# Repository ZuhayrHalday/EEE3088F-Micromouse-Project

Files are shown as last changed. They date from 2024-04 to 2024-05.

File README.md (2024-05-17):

# MicroMouse Project: Sensing and Power Subsystems

Welcome to the MicroMouse Project repository! The problem this entire project deals with is to design, build, and test a fully-functioning MicroMouse robot. Akin to the mice in the famous Kerplunk Experiments, a MicroMouse robot should be able to solve a maze using the shortest and fastest route possible. This README provides an overview of the project and subsystem descriptions.

## Project Overview

The goal of this project is to build key subsystems for a simplified MicroMouse, a maze-solving robot. These will be designed, manufactureed, and tested during the course of a semester.

## Subsystems

### 1. Power Subsystem (more info [here](https://github.com/ZuhayrHalday/EEE3088F-Micromouse-Project/tree/main/Power%20Subsystem))
- **Purpose:** Provide power to the entire system.
- **Key Functions:**
  - Operate two motors (each drawing up to 200mA).
  - Charge the battery from a 5V input.
  - Provide battery voltage information to the processor.
  - Include an ON/OFF switch with specific power draw requirements.
- **Connections:**
  - JST PH 2mm pin pitch connector for the battery.
  - 2x8 (2.54mm pin pitch) pin header for interfacing with the motherboard.<br />
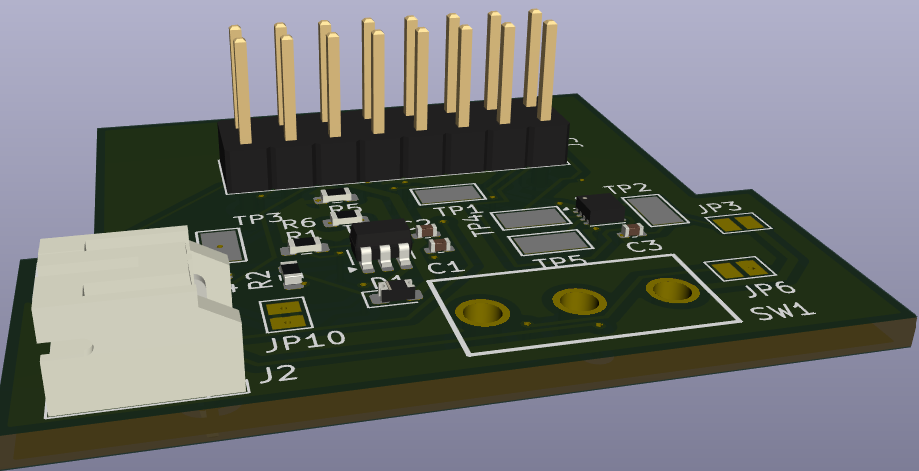
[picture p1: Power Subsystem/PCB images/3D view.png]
  <br />

### 2. Sensing Subsystem (more info [here](https://github.com/ZuhayrHalday/EEE3088F-Micromouse-Project/tree/main/Sensing%20Subsystem))
- **Purpose:** Detect obstacles in the robot's path.
- **Key Functions:**
  - Detect obstacles in front and on the sides of the robot using infrared LED's and photodiodes to sense reflective obstacles.
  - Use power-saving features when not in operation.
  - Provide reliable detection data to the processor.
  - Interface with processor LEDs to indicate detected obstacles.
- **Connections:**
  - 2x14 (2.54mm pin pitch) pin header for interfacing with the motherboard.<br />
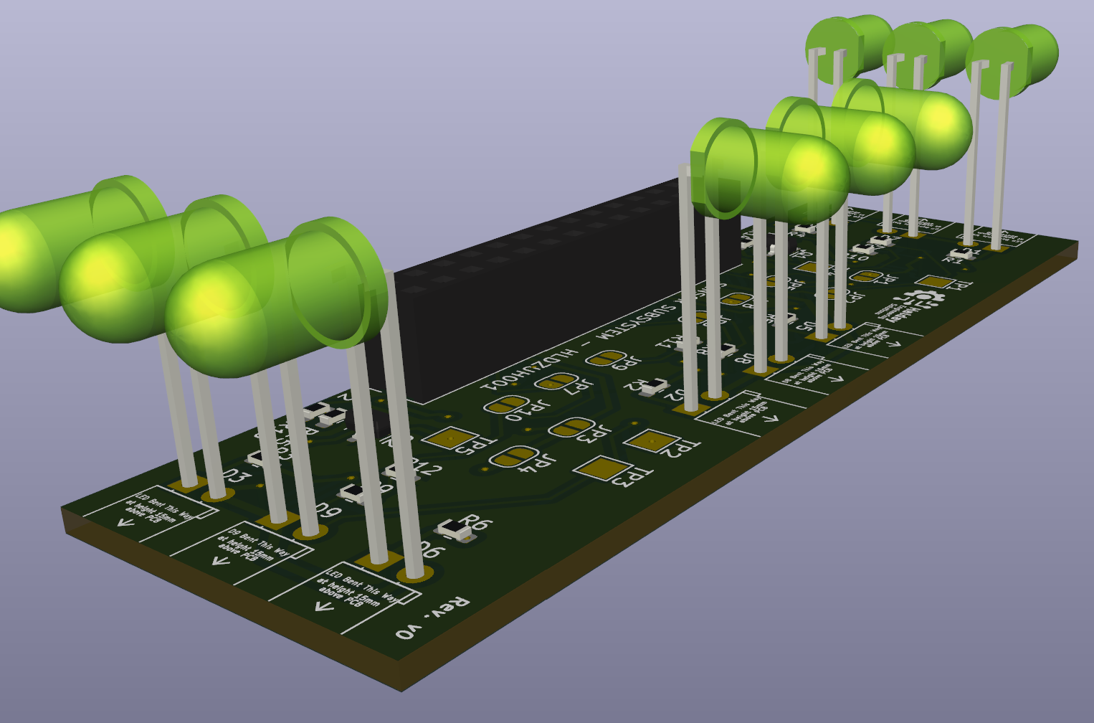
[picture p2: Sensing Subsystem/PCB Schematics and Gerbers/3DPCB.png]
  <br />

### 3. The Motherboard
The Motherboard houses all subsystems and addresses the movement and ‘brain’ aspects of the project. The
wheels and motors of the MicroMouse are attached to the Motherboard PCB, which also mounts an STM32L476
microcontroller to manage input and output logic. Pin headers are provided for interfacing with other subsystems. This subsystem has been provided beforehand, and was not designed as a part of this project.

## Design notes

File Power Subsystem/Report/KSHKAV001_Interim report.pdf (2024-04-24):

# Interim Design Report

Micromouse Power Subsystem


Prepared by:
Kavya Kaushik

Prepared for:
EEE3088F
Department of Electrical Engineering University of Cape Town

April 21, 2024

# Declaration

1. I know that plagiarism is wrong. Plagiarism is to use another’s work and pretend that it is one’s own.
2. I have used the IEEE convention for citation and referencing. Each contribution to, and quotation in, this report from the work(s) of other people has been attributed, and has been cited and referenced.
3. This report is my own work.
4. I have not allowed, and will not allow, anyone to copy my work with the intention of passing it off as their own work or part thereof.

Sign:

Date: 21 April 2024

ii

# Contents

1 Introduction | 1
2 Requirements Analysis | 2
3 Subsystem Design | 5
4 Acceptance Testing | 10

iii

# Chapter 1

# Introduction

### 1.1 Problem Description

The project focuses on the development of an autonomous maze-solving robot, commonly known as a micro-mouse. the project aims to integrate power, sensing and control to operate this robot. This report is focused on the design of the power subsystem, with the goal of supplying uninterrupted regular current to the micro-mouse to ensure its safe and effective operation. The design involves considering specific design requirements and specifications while comprising of integration with the sensing and control subsystems while adhering to the specified limitations.

### 1.2 Scope and Limitations

Scope | Limitations
Component selection and sizing: Select appro-priate components considering such as voltage, current ratings, energy capacity, sizing, effi-ciency and costs | Limited budget which impacts the cost and quality of components that can be used
Power distribution and regulation: Ensuring stable voltage supply to various subsystems and components of the robot, depending on specifications of the components and specifica-tions of the rest of the system for integration | Constraints on the size of the components to ensure it fits onto the motherboard and along with the other subsystems
Implement a battery management system to control the charging and discharging for opti-mal battery performance | Limitations to the energy capacity of the sys-tem and discharge rates of the battery as per requirements
Ensure that the power subsystem can be inte-grated with the remaining system | Constraints about placement and connections of the other subsystems to ensure integration
Implement testing and fault tolerance mecha-nisms to ensure reliability of the circuit and to verify its functionality and performance during different conditions. | Limitations resources for sufficient testing and validation

Table 1.1: Scope and Limitations of the Power Subsystem

### 1.3 GitHub Link

Project GitHub repository: Github Link (https://github.com/ZuhayrHalday/EEE3088F-Micromouse-Project)

# Chapter 2

# Requirements Analysis

### 2.1 Requirements

The requirements for a micro-mouse power module are described in Table 2.1.

Table 2.1: User and functional requirements of the power subsystem.

Requirement ID | Description
FR01 | Supply power to the battery using voltage from a logic-based micro controller power supply to charge the battery
FR02 | Regulate the charging and discharging of the battery to ensure overcharging, temperature monitoring and over-discharge protection by regulating the current drawn from the battery
FR03 | Maximise battery life by allowing minimal power consumption
UR01 | Supply regulated current to both motors to drive them
UR02 | Provide an analogue signal that indicates the battery’s state of charge from the battery voltage that can be sent to the ADC of the micro controller
UR03 | Contains a switch to turn the power supply ON/OFF
FR04 | The PCB board fits onto the pin headers of the motherboard
FR05 | The PCB designed with an size suitable for the micro mouse robot
UR04 | The PCB cost is within the budget specified
UR05 | All components in stock with JLCPBCB
FR06 | Battery has a maximum and minimum current draw in ON and OFF state

### 2.2 Specifications

The specifications, refined from the requirements in Table 2.1, for the micromouse power module are described in Table 2.2.

Table 2.2: Specifications of the sensing subsystem derived from the requirements in Table 2.1.

Specification ID | Description
SP01 | The battery used is a LiPo 800mAh 3.7V battery
SP02 | The battery is charged is a 5V input pin from a microcontroller
SP03 | The battery is kept at a max discharge rate of 0.5C(capacity) implying that a fully charged battery takes 2 hours to fully discharge
SP04 | The maximum current drawn by the battery is 400mA
SP05 | The circuit needs to supply current to two motors with a maximum current draw of 200 mA each

2.3. Testing Procedures
Specification ID | Description
SP06 | The analog output needs to be within the range of to meet the STM32L476 microcontroller’s ADC range
SP07 | The battery can only draw less than 500uA when the switch is in the OFF state
SP08 | The battery can draw the peak current of 400mA during the ON state of the switch
SP09 | A JST PH 2mm pin pitch is used as the connector for the battery
SP10 | A 2x8 (2.54mm pin pitch) pin header is for the power subsystem
SP11 | The connector needs to be centered in a tab and have a maximum width of 35mm and a minimum height of 18mm
SP12 | The circuit uses PWM integration with microcontroller
SP13 | Both PCB boards need to be manufactured within $30

### 2.3 Testing Procedures

A summary of the testing procedures detailed in chapter 4 is given in Table 2.3.

Table 2.3: Testing procedures for Power Subsystem

Acceptance Test ID | Description
AT01 | Battery Voltage supply check
AT02 | Switching circuit ON state
AT03 | Switching circuit OFF state
AT04 | Input pin connection of 5V
AT05 | Battery charging operation
AT06 | Analog output supply of battery state of charge
AT07 | Current output into motors test
AT08 | Power supply of motors test
AT09 | PCB dimensions test
AT10 | Project budget test

2.4. Traceability Analysis

### 2.4 Traceability Analysis

The show how the requirements, specifications and testing procedures all link, Table 2.4 is provided.

Table 2.4: Requirements Traceability Matrix

# | Requirements | Specifications | Acceptance Test

1 2 3 4 5 6 7 | FR01 FR02, FR03, FR06 UR01 UR02 FR04 UR04 FR05 | SP01, SP02 SP03, SP04, SP07, SP08 SP05 SP06 SP10 SP13 SP11 | AT01, AT04 AT02, AT03, AT05 AT07, AT08 AT06 AT09 AT10 AT09

Traceability Analysis 1 - FR01 is this from which SP01, SP02, can be derived. To test this AT01, AT04 is suggested to ensure successful operation of the battery

Traceability Analysis 2 - From FR02,FR03, FR04, SP03, SPO4, SP07 and SP08 can be derived to properly check the switching circuit and charging and discharging.

Traceability Analysis 3 - From UR01, SP05 can be derived to check the successful operation of motors which can be tested using AT07, AT08

Traceability analysis 4 - From UR02, SP06 can be derived and the output analoge signal which can be tested with AT06.

Traceability Analysis 5 - From FR04 SP10 can be derived and test AT09 can be conducted to test the implementation of pin header

Traceability analysis 6 - From UR04, SP13 can be derived to check the budgeting of PCB which can be tested using A10

# Chapter 3

# Subsystem Design

### 3.1 Design Decisions

### 3.1.1 Battery Management System

The battery used as per specification , and has a voltage range between 3.0V to 4.2V with a recommended Lithium Polymer charger[[reference]. The battery management system needs to consider the requirements such to ensure functionality and circuit protection, for which a battery management IC can be used.

Based on specification SP01, the battery management ICs that can support all functionality and are in stock are listed in Table 3.1.

Table 3.1: Component specifications for the battery management system
Item | Component | Voltage regulation | Charge current | Cost
1 | MCP73831T-2ATI/OT | 4.2V, 4.35, 4.40V, 4.50V | 15mA to 500mA(prog*) | 0.9945
2 | BQ24295 | 4.55 V – 5.5 V | 1792mA for V = 3.8V | 0.7635
3 | MCP73833/4 | 4.2V, 4.35V, 4.4V, 4.5V | 1A (prog*) | 1.5330
4 | MCP73837/8 | 4.20V, 4.35V, 4.4V or 4.5V | 15 mA – 1000 mA (prog*) | 2.7900

*prog means the value is programmable

From Table 3.1, it can be seen that Component 3 draws a much larger current compared to the other three components, amongst which Component 1 is the cheapest. Therefore the MCP73831T component is finalised as the battery charging IC since it supports the voltage range of the battery which is 4.2V, it can handle the current drawn by the battery which is 400mA and it is the most cost-effective.

The datasheet is used to implement the circuit accoridng to specified resistors, LEDs and capacitors.

### 3.1.2 Motor Driver ICs

A motor driver IC is the most efficient way to power a motor driver, as it protects the microcontroller and battery power supply from getting damaged by the current drawn by the motors (https://www.wellpcb.com/what-is-motor-driver.html).

The implementation of an H-bridge can form a crucial component to drive the motors such that a voltage can be applied across the motor in either direction and the motors can be powered independently using control signals. (https://docs.onion.io/omega2-maker-kit/maker-kit-servo-h-bridge.html). A low voltage H-bridge can controol current flow, regulate current amplification and implement other

3.1. Design Decisions

protection features. Based on the specification SP05 and UR01 the Motor driver ICs considered are listed in Table 3.2.

Table 3.2: Motor driver integrated chip specifications
Component | Drive Current | Driver type and output | Stock | Cost
DRV8834 | 1.5A | Dual bridge and can drive 2 DC motors | 2419 | 0.9660
DRV8837DSGR | 1.8A | H-Bridge and can drive 1 DC motor | 67946 | 0.1235

To abide by costs and to ensure a high current capacity the DRV8837DSGR motor driver is chosen. The motor driver can only drive 1 motor hence two drivers are used in the circuit design. The drivers are powered by the battery and supply power to the motors for output.

### 3.1.3 Circuit Switch

The circuit switch needs to comply with requirements UR03 anD specifications SP07 and SP08. The circuit needs to ensure that the battery is completely disconnected in the ON state. The spec of two battery pins needs to be considered.

r0.4

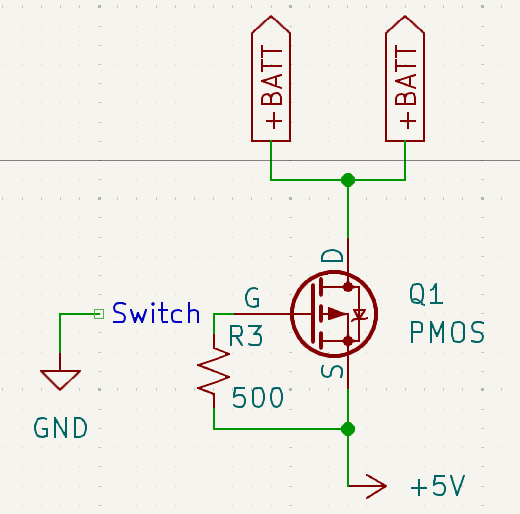
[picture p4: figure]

Design A - MOSFET Switch

A p-channel MOSFET can be used in enhancement mode to design high-current switches when configured as can be seen in subsection 3.1.3. When the switch is ON, current flows through the switch and into the battery pins and the circuit is is ON state. However, when the switch is disconnected, no current flows through the MOSFET and the circuit is in its OFF state.

The MOSFET used is SI2319CDS which can handle sufficient drain current to handle the battery current of 400mA. The switch used here is the surface mount SSAJ110100 which can carry a 10mA current at its gate.

Design B - A push/pull switch device

This circuit requires a switch that can handle the battery current and upon looking at available components on JLCPCB and avialable footprints on KiCad the SS-12D10L5 switch is chosen. Its specifications are given in Table 3.3

Based on Design A and Design B design A is chosen due to its simplicity, the use of fewer components reduces the risk of component failures and circuit costs. Design B also uses fewer connections thus avoiding the risk of faulty traces within the PCB.

3.2. Failure Management

Table 3.3: A single pole double throw switch specifications
Component | Current rating | Stock | Cost
SS-12D10L5 | 3A | 41376 | 0.2847

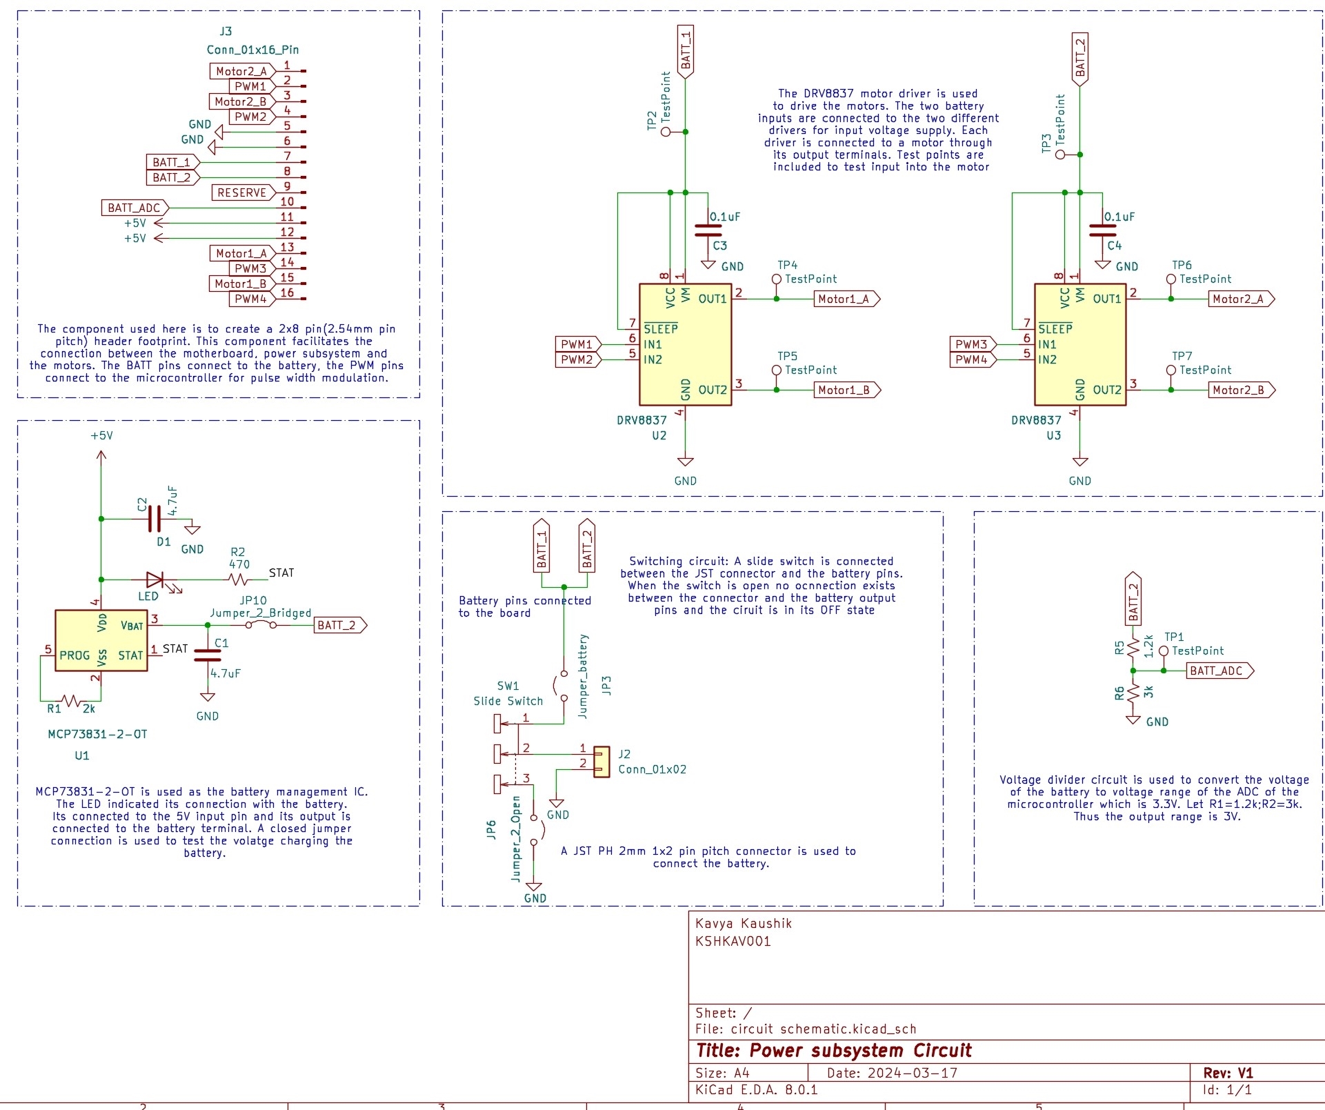
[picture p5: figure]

Figure 3.1: Final circuit schematic

### 3.1.4 Final Design

The final solution of the power subsystem is obtained by combining the final design decisions made in the sections above. The battery management system, motor driver system, switching circuit and analogue signal supply circuit combined together effectively meet the requirements of the project. The final circuit schematic can be seen in Figure 3.1

### 3.2 Failure Management

The failure management methods for the Power subsystem are listed in Table 3.4

3.3. System Integration and Interfacing

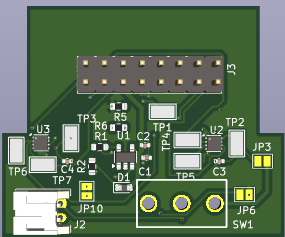
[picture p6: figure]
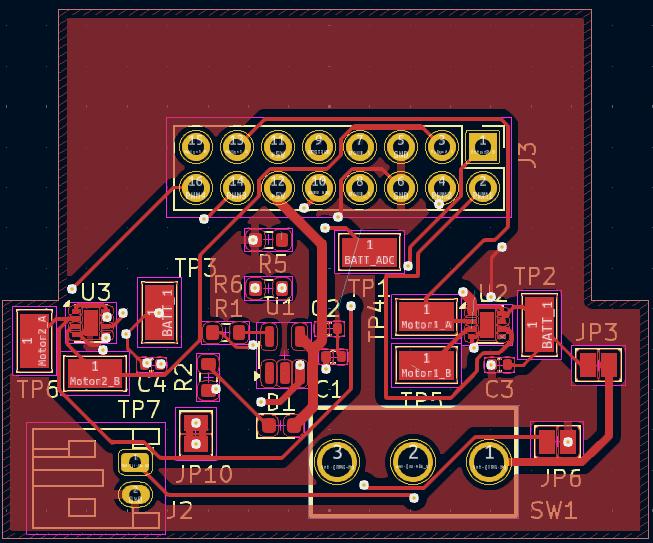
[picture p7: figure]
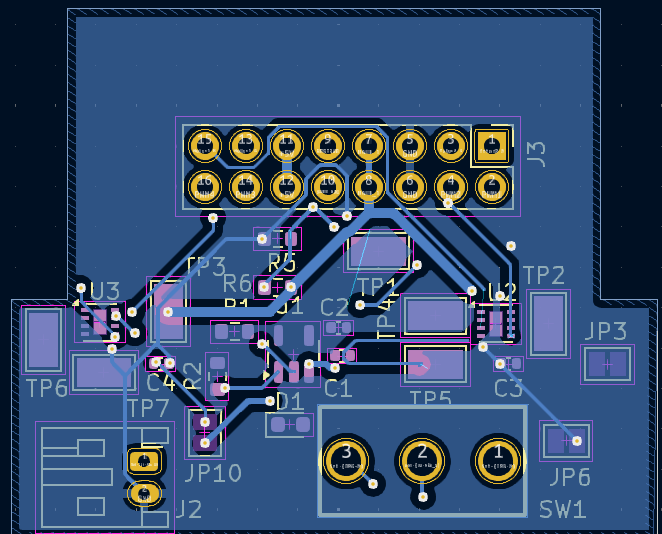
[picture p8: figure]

(a) Front PCB | (b) Back PCB | (c) 3D PCB

Figure 3.2: PCB

Table 3.4: Failure management methods of Power subsystem
Failure management method | Description
Component Placement strategy | Strategic placement of components for shorter trace lengths and to minimise signal interference
Battery charging failure | Jumper cables used to check voltage and current supply of battery charger IC
Switching circuit failure | Open jumper cable connected with switch to allow a direct connection incase switch doesn’t operate as expected.
Test points | Testpoints used to check current at output of motor drivers to cater for cases where the output requirements for motor driver are not met.
Component overload protection | Implement current-limiting resistors and capacitors to prevent excessive control flow
Component failure management | Include additional parallel resistor and capacitor paths to rectify any issues due to component failure (suggested method not included in current circuit)
DRC and ERC checks | Conduct design and electrical rule check on KiCad to ensure electrical integrity and detect any layout errors
Trace width optimisation | Set trace widths of PCB depending on the voltage carried by the traces to avoid overloading.

### 3.3 System Integration and Interfacing

The power subsystem is integrated with the rest of the micromouse system as per ??

Table 3.5: Interface Pin Connections and Description
Interface | Pin* Connections | Description
1001 | • Pin 1 - Output terminal 1 of Motor Driver A • Pin 3 - Output terminal 2 of Motor Driver A | Connect Motor Driver A to mother-board.
1002 | • Pin 2 - PC6-9 (PWM1) • Pin 4 - PC6-9 (PWM2) | Interface input logic signal with Mo-tor Driver A
1003 | • Pin 5 - GND • Pin 6 - GND | Ground connection of subsystem

Continued on next page

3.3. System Integration and Interfacing

Table 3.5 continued from previous page
Interface | Pin* Connections | Description
1004 | • Pin 7 - BATT (Battery Terminal) • Pin 8 - BATT (Battery Terminal) | Connect to the two terminals of the battery
1005 | • Pin 9 - PD7 | Reserve pin, can be used for addi-tional connection
1006 | • Pin 10 - ADC | Output analog signal to ADC of mi-crocontroller
1007 | • Pin 11 - 5V • Pin 12 - 5V | Connect to input power supply (pos-itive terminal)
1008 | • Pin 13 - Output terminal 1 of Motor Driver A • Pin 15 - Output terminal 2 of Motor Driver B | Connect Motor Driver B to mother-board.
1009 | • Pin 14 - PC6-9 (PWM3) • Pin 16 - PC6-9 (PWM4) | Interface input logic signal with Mo-tor Driver A
1010 | • JST-PH Pin connector - Battery | Connect the battery connector to the terminals of the battery

*pin refers to the pins of the 2x8 pin header
*PWM - pulse width modulation; logic signal of microcontroller

### 3.3.1 System Inerfacing Diagram

The diagram to visualise the system integration is shown in Figure 3.3

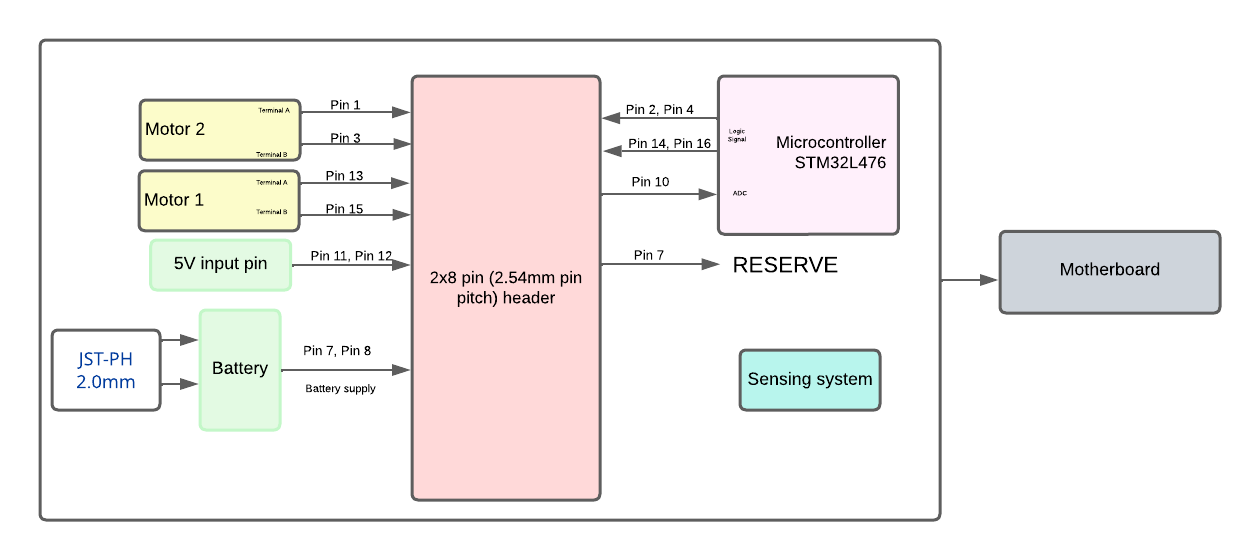
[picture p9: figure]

Figure 3.3: System Interfacing diagram

# Chapter 4

# Acceptance Testing

The testing procedures to test the performance of the PCB are listed in Table 4.1

Table 4.1: Subsystem acceptance tests

Test ID | Description | Testing Process | Pass/Fail Criteria
AT01 | Battery voltage require-ment | • Use a multimeter to check if the battery is connected and check its voltage reading | • Pass - The voltage read-ing is 3.7V • Fail - The reading is not 3.7V
AT02 | Switching circuit ON state | • Toggle the switch to ON • Use the jumper cable at the switching circuit output to measure current drawn by bat-tery | • Pass - The maximum current reading is 400mA • Fail - The current read-ing is null or more than 400mA
AT03 | Switching circuit OFF state | • Toggle the switch OFF • Use the jumper cable at the Switching circuit output to battery current drawn | • Pass - The maximum current drawn by the battery is 500uA • Fail - The current is more than 500uA
AT04 | Input pin connection | • Use a multimeter to take volt-age reading of input pin from the pin header | • Pass - Reading of 5V • Fail - Reading is not 5V

Continued on next page

Table 4.1 – continued from previous page
Test ID | Description | Testing Process | Pass/Fail Criteria
AT05 | Battery charging IC | • Put the circuit in ON state us-ing the switch • Look at the LED to check if the IC is charging the battery | • Pass - The LED light is ON • Fail - The LED light is off
AT06 | Analog output of bat-tery | • Read the output voltage of voltage divider circuit using a multimeter | • Pass - If the reading is in the range of 3.3V • Fail - Reading is null or less than 3.3V
AT07 | Current drawn by mo-tors | • Use a multimeter to read cur-rent using the test points at the input of the motor driver IC • Repeat for both driver ICs | • Pass - The current read-ing is a maximum of 200mA for each driver IC • Fail - The current is null or more than 200mA
AT08 | Operation of Driver ICs | • Use the test points to check the output current at the driver IC using a multimeter • Repeat for both output termi-nals for both driver ICs | • Pass - Maximum current of 200mA • Fail - Current greater than 200mA or no cur-rent reading
AT09 | Dimensions of PCB board | • Measure the width of the tab • Measure height of the tab | • Pass - height > 18mm and width < 35mm • Fail - Height < 18mm and/or Width > 35mm
AT10 | Budget | • Calculate total cost of manu-facturing PCB using Bom and a maybe through a receipt | • Pass - Cost of PCB for 2x mounted boards is less than $30 • Fail - Cost of PCB is more than $30

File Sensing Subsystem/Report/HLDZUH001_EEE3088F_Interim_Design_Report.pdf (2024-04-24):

# Interim Design Report

Micromouse Sensing Subsystem


Prepared by:
Zuhayr Halday

Prepared for:
EEE3088F
Department of Electrical Engineering University of Cape Town

April 21, 2024

# Declaration

1. I know that plagiarism is wrong. Plagiarism is to use another’s work and pretend that it is one’s own.
2. I have used the IEEE convention for citation and referencing. Each contribution to, and quotation in, this report from the work(s) of other people has been attributed, and has been cited and referenced.
3. This report is my own work.
4. I have not allowed, and will not allow, anyone to copy my work with the intention of passing it off as their own work or part thereof.

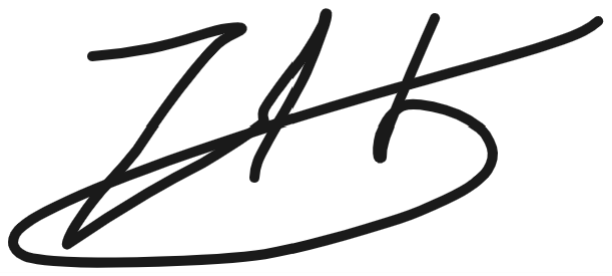
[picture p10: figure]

April 21, 2024

Name Surname | Date

ii

# Contents

1 Introduction | 1
2 Requirements Analysis | 3
3 Subsystem Design | 6
4 Acceptance Testing | 11

iii

# Chapter 1

# Introduction

### 1.1 Problem Description

The problem the entire project deals with is to design, build, and test a fully-functioning MicroMouse robot. Akin to the mice in the famous Kerplunk Experiments, a MicroMouse robot should be able to solve a maze using the shortest and fastest route possible.

While the greater problem of building a MicroMouse may seem simple, it is quite a complex task which must be broken down into many smaller and more manageable sub-tasks. To do so, a fundamental question must be asked: ‘What does a robot (or any entity) require in order to solve a maze?’ The four basic necessities to addressing the greater project are found by answering this question, that being: the ability to move, to detect obstacles such as maze walls, the logical capability or ‘brain’ to decide how the robot moves based on what it detects, and the ability to power itself while solving the maze. By applying the philosophy of Systems Engineering and principle of modular design, these smaller problems can be addressed by assigning each to different subsystems: Power, Sensing, and the Motherboard.

The Motherboard not only houses all other subsystems, but addresses the movement and ‘brain’ aspects of the project, as the two wheels and motors of the MicroMouse are attached to the main Motherboard PCB, and in order to deal with its input and output logic capabilities, an STM32L476 microcontroller is also mounted onto the Motherboard, with pin headers to facilitate connection and interfacing between other subsystems.

The Power subsystem is in charge of directing power from a battery to all subsystems and motors of the MicroMouse, and conversely, charging said battery when the robot is plugged into an external power source.

The third and final subsystem, Sensing, will be the part of the MicroMouse that is able to detect the presence and distance from the walls of the maze and send the information it detects to the microcontroller, in order to determine the direction in and speed at which the robot should traverse the maze. This report specifically focuses on the problem of designing, building and testing the Sensing subsystem.

### 1.2 Scope and Limitations

The scope of this specific project only concerns the Sensing subsystem described above, its interactions with the environment around it, and its ability to interface with other subsystems. Intricate details of other subsystems are not included in this scope.

The biggest limitations of this project are the size of the Sensing PCB, and the components from which

1.3. GitHub Link

it is able to made up of. Firstly, in order to not obstruct the turning radius of the wheels of the robot, the Sensing PCB is limited to a width and length of roughly 85mm and 30mm respectively. Secondly, the components of said PCB must include a 2x14, 2.54mm pin pitch socket in order to connect to the Motherboard subsystem. These components are only able to be comprised of available parts from JLCPCB, and must have a total manufacturing cost of $15 for a single board.

### 1.3 GitHub Link

The GitHub repo for this project is available here. (https://github.com/ZuhayrHalday/EEE3088F-Micromouse-Project)

# Chapter 2

# Requirements Analysis

### 2.1 Requirements

The requirements for the micromouse sensing subsystem are described in Table 2.1.

Requirement ID | Description
REQ01 REQ02 REQ03 REQ04 REQ05 REQ06 REQ07 REQ08 REQ09 | Each subsystem sensor is able to detect a wall or reflective object Subsystem has sensors on the left, right, and front sides of the micromouse Subsystem has pin sockets to interface with the motherboard and processor Subsystem is able to be powered by a battery Outputs of each sensor are repeatable and continuous Subsystem PCB size must not obstruct wheels and must fit on the motherboard Output of each sensor is in the form of an analogue voltage signal Subsystem only uses JLCPCB components Manufacturing cost of PCB’s are within budget

Table 2.1: Requirements of the sensing subsystem.

### 2.2 Specifications

The specifications, refined from the requirements in Table 2.1, for the micromouse sensing subsystem are described in Table 2.2.

Specification ID | Description
SP01 | Each subsystem sensor makes use of infrared (IR) LED’s and photodiodes to
| detect obstacles
SP02 | Sensors should only detect obstacles that are 6-10 cm away, and should have
| distinguishable outputs within that distance range
SP03 | PCB includes a 2x14, 2.54mm pin pitch socket to connect to the motherboard
SP04 | Subsystem is able to be powered by a 3.7V 1S1P 18650 battery
SP05 | Outputs of each sensor are reliable and not affected by external light
SP06 | Subsystem PCB should have a width and length of no greater than 85mm and
| 30mm respectively
SP07 | Output signal of each sensor should be within 0.8-1.5V, so as to not drain the
| battery
SP08 | Subsystem makes use of mostly basic components, avoiding extended
| components where possible
SP09 | Manufacturing cost of a single PCB is $15 or lower

Table 2.2: Specifications of the sensing subsystem derived from the requirements in Table 2.1.

2.3. Testing Procedures

### 2.3 Testing Procedures

A summary of the testing procedures detailed in chapter 4 is given in Table 2.3.

Test ID | Description
AT01 | IR LEDs Power on
AT02 | IR Photodiodes Power on
AT03 | Subsystem output changes at the left, right, and front of the board
AT04 | Connects to motherboard
AT05 | Powers on
AT06 | Accepted by JLCPCB

Table 2.3: Acceptance Testing Summary for Subsystem

### 2.4 Traceability Analysis

The show how the requirements, specifications and testing procedures all link, Table 2.4 is provided.

# | Requirements | Specifications | Acceptance Test

1 2 3 4 5 6 7 8 9 | REQ01 REQ02 REQ03 REQ04 REQ05 REQ06 REQ07 REQ08 REQ09 | SP01 SP02 SP03 SP04 SP05 SP06 SP07 SP08 SP09 | AT01, AT02 AT03 AT04 AT01, AT02, AT05 AT03 AT04 AT03 AT06 AT06

Table 2.4: Requirements Traceability Matrix

### 2.4.1 Traceability Analysis 1

SP01 was derived from REQ01, as IR proximity detection circuits are popular for object detection robotics. AT01 and AT02 test if these IR components function as intended to satisfy REQ01 and SP01.

### 2.4.2 Traceability Analysis 2

SP02 was derived from REQ02, since the micromouse should be able to see walls in all forward directions, but should not be hesistant to move when detecting a wall from far away. AT03 was made to test each side’s sensor only produces an output signal when 6-10cm away from an obstacle/wall.

2.4. Traceability Analysis

### 2.4.3 Traceability Analysis 3

SP03 was derived from REQ03, as this is the connector needed to mount the subsystem to the motherboard, allowing the microcontroller to interface with the subsystem. AT04 will test this, as if the PCB does not fit onto and connect to the microcontroller, the micromouse will not function.

### 2.4.4 Traceability Analysis 4

SP04 was derived from REQ04, as the battery specified to be used to power the micromouse was given. AT01, AT02, and AT05 test this, as this will indicate whether or not components are being powered, and whether the power drain is too much for the battery to handle.

### 2.4.5 Traceability Analysis 5

SP05 was derived from REQ05, as outputs should consistently detect obstacles in real time, and should not falsely detect obstacles due to external light. AT03 tests this as it monitors the output signal of the subsystem when obstacles and external light is present.

### 2.4.6 Traceability Analysis 6

SP06 was derived from REQ06, as this is the space allocated to the sensing subsystem on the motherboard PCB. AT04 will test this, as the subsystem will not connect to the motherboard if it does not fit, or obstructs the wheels of the micromouse.

### 2.4.7 Traceability Analysis 7

SP07 was derived from REQ07, as the output signal is generated by the photodiode drawing current from the battery, and should not drain the battery too fast. AT03 tests this by monitoring the current draw and voltages of each output signal to make sure it is within a suitable range.

### 2.4.8 Traceability Analysis 8

SP08 was derived from REQ08, because there is a high chance of the subsystem cost going over-budget when using many extended components from JLCPCB. AT06 tests this, as one is able to see the total cost of manufacturing when submitting a PCB to JLCPCB.

### 2.4.9 Traceability Analysis 9

SP09 was derived from REQ09, as this was the budget allocated to the sensing subsystem. AT06 tests this, as one is able to see the total cost of manufacturing when submitting a PCB to JLCPCB.

# Chapter 3

# Subsystem Design

### 3.1 Design Decisions

While the initial circuit layout remained the same throughout all versions of the design, component choices differed greatly, especially when taking into account component stock and pricing from JLCPCB. All IR components demanded extended component fees, which greatly scaled down the size of the subsystem. On top of this, many ideal components were out of stock. Compromises had to be made when making design decisions, but were done while still keeping all specifications and requirements in mind.

### 3.1.1 IR LED Emitter Circuit

In accordance with SP01 in section 2.2, an IR LED circuit needed to be part of the design, and in accordance with REQ02, these LEDs needed to have directionality. Immediately, this elminated the consideration of using any surface-mounted IR LEDs, as there would be absolutely no way to manipulate the surface of the PCB to face the left, right, and front of the micromouse. Therefore, only through-hole LEDs were considered.

Expanding on the property of directionality, radial LEDs were ideal, as the angle of half-intensity for side-emitting was much smaller than those of radial LEDs. Outputs of the sensor circuit are greatly dependent on the intensity of light emitted by the IR LEDs, so in order to take SP05 and SP07 (section 2.2) into account, only radial through-hole IR LEDs were considered.

Due to limited stock and budget constraints, this narrowed the selection down to just two IR LEDs: the TSAL6200 and the TSAL4400. The pros and cons of each component were then weighed against each other, as seen in Table 3.1: While there were not many differences between these IR LEDs, the

TSAL6200 | TSAL4400
Pros | Cons | Pros | Cons
Cheaper | Smaller half-intensity angle | Larger half-intensity angle | More Expensive
Higher radiant intensity | | | Lower radiant intensity

Table 3.1: TSAL6200 vs TSAL4400

differences that mattered the most were cost effectiveness, and radiant intensity, and the TSAL6200 was the better choice in both of these categories. Therefore, the TSAL6200 was used in the IR LED Emitter Circuit. (Note: Two TSAL6200 LED’s will be used per side of the PCB to ensure adequate light intensity)

3.1. Design Decisions

Calculations

As this in an LED, a current-limiting resistor is required to safely power the LED. Due to the maximum current rating of 100mA for the TSAL6200, calculations are needed in order to find a resistance value which will safely limit the current under the maximum rating:

RLED =

(VS − VF )

Imax

Using the known source voltage of 3.7V (1S1P 18650 battery), and the maximum forward voltage drop and maximum current, as listed in the TSAL6200 datasheet:

RLED =

(3.7 − 1.6)
100 ∗ 10⁻³

= 21Ω

Therefore, any resistor larger than 21Ω will suffice. For this circuit, 39Ω was used as the current-limiting resistor for each LED, resulting in ILED = 60mA.

### 3.1.2 IR Photodiode Sensor Circuit

In order to generate some sort of output signal from merely an IR LED, an IR photodiode was necessary. As IR light reflects off of obstacles, a reverse-biased IR photodiode is able to detect the reflected IR light, and generate a current dependent on the intensity of the reflected light. Three IR photodiodes were used in the subsystem, one for the left, right, and front of the PCB.

Unlike the IR LEDs, the photodiode should have as small of a viewing angle as possible, so as not to detect IR light from any direction other than the one it faces. The photodiode should ideally have a daylight blocking filter as well, in order to reduce the disturbance from external light.

Based on all of the above factors, the ‘SFH’ line of photodiodes from Osram are ideal, as all of these photodiodes have a roughly >90% spectral sensitivity to light of wavelength 940nm, which is the wavelength of light emitted by our chosen IR LEDs. On top of having its built-in daylight blocker, this sensitivity is also very low for lower wavelengths of light, further reducing the impact of external light to the sensor. After considering the entire line of available SFH photodiodes, the SFH213FA was selected, due to it being one of the only photodiodes from this line still in stock, while having the lowest viewing angle out of all of the in-stock options.

Calculations

Using the Radiant Power curve of the TSAL6200 from its datasheet, we can see that a forward current of 60mA results in the LED emitting light with power Pradiant = 25mW. The Light Intensity formula can now be applied:

IN =

Pradiant
4πr²
Calculating the radial light intensity 60mm (close distance) away from the LED:

∴ IN =

25 ∗ 10³
4π(6cm)

2

= 552.6µW/cm²

This light intensity will be used in order to determine the photocurrent of the SFH213FA, when receiving IR light from the TSAL6200. Using the Photocurrent Curve of the SFH213FA from the

3.1. Design Decisions

datasheet, it can be determined that a light intensity of 552.6µW/cm²
corresponds to a photocurrent of:IP ≈ 22µA

With this current value, we can determine the voltage drop across a load resistor RL connected in series with the SFH213FA. This is a simple calculation, and choosing an E12 resistance value of 47kΩ gives an output voltage:
Vout = I ∗ R = (22 ∗ 10⁻⁶
)(47000) = 1.03V

Therefore, when the sensor fully reflects all light from the IR LED from 6cm away, the system should have an output of 1.03V at maximum, when taking into account materials that allow IR to pass through or other external factors.

According to the Light Intensity equation, Pradiant will decrease as distance increases, meaning less light intensity, and hence less photocurrent as the sensor moves further away from the reflective obstacle. This means that the selected photodiode is perfect for meeting the SP07 specification for the output signal of the sensor.

### 3.1.3 Transistor Switch Circuit

While not making a large difference to how the subsystem sensors will function, the design choice to use an NPN BJT as a switch for the IR LEDs is important in reducing the power consumption of the subsystem, allowing for longer battery life. The emitter of the NPN will be connected to the end of the IR LED Emitter circuit, and its base will be connected to one of the PWM pins of the microcontroller. This is done so that the LEDs will pulse rapidly, conserving battery life whenever it is turned off, but still pulsing fast enough to be detected by the photodiode sensors. The TSAL6200 selected previously is also very suitable for high-pulse operation, and will not be damaged.

The 2222A NPN BJT was selected as the transistor, since its maximum current rating is able to handle the current from up to five TSAL6200s operating at 60mA simultaneously. This is also a very versatile and cheap transistor, and does not disagree with any specifications or requirements. A base resistor of 1kΩ will be used with the 2222A, and the PWM pin from the microcontroller will then control the base voltage of the 2222A, rapidly pulsing the IR LEDs.

### 3.1.4 Final Design

The final design for the Sensing subsystem is comprised of the three aforementioned circuits. All components are suitable for use with one another and within the circuit. All absolute maximum and minimum ratings were checked and all selected components have suitable ranges for operation within the subsystem. The final design schematic and PCB can be seen below. (Note: All datasheets mentioned above can be accessed from the GitHub repo under Sensing Subsystem/Datasheets)

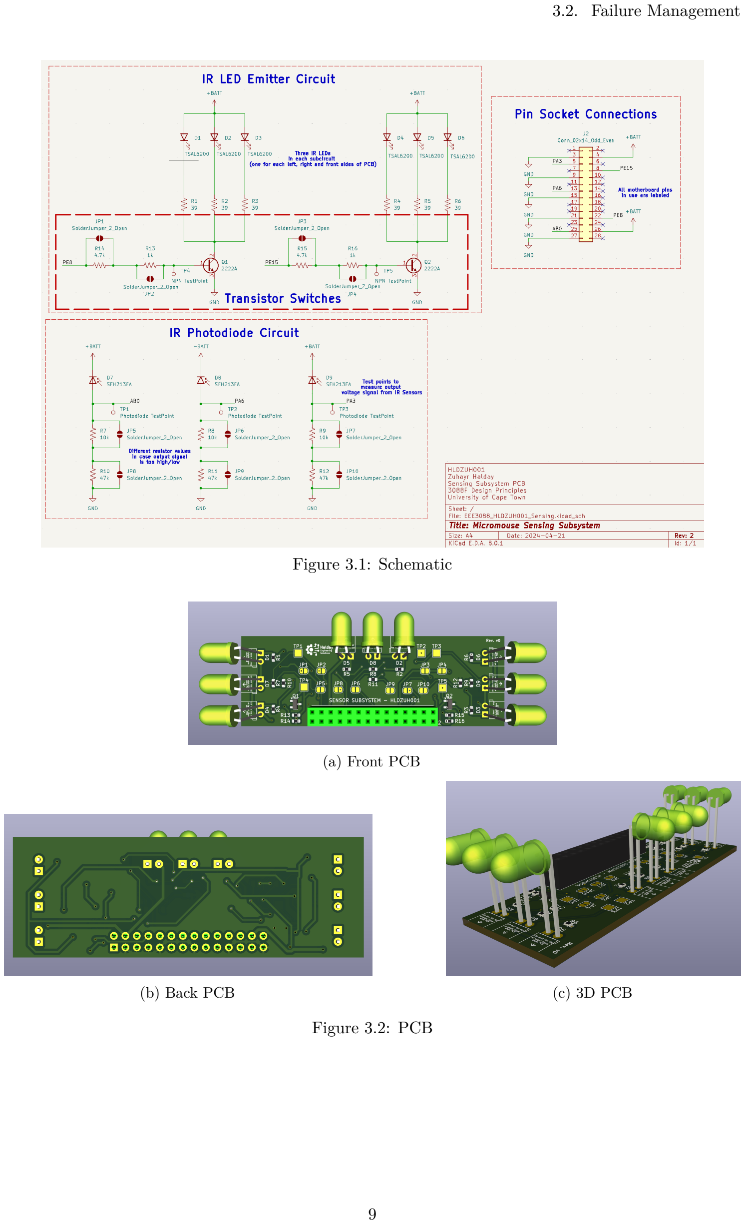
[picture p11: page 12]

3.2. Failure Management

Figure 3.1: Schematic

(a) Front PCB
(b) Back PCB | (c) 3D PCB

Figure 3.2: PCB

3.2. Failure Management
Name | Description
Modular IR LED Circuits | Six IR LEDs have been split up into two separate circuits of three each (one for each side of the board). This is done so that if one circuit fails, there will still be at least one functioning IR LED and photodiode on each side of the board.
PCB Thermal Management | The width of all PCB tracks vary depending on how much current is expected to travel through each track. Wider tracks correspond to higher current, ensuring the PCB stays safe from thermal impacts.
Redundant Resistors | In the cases where exact resistor values were not able to be calculated, multiple different resistors were added to the PCB, with solder jumpers connecting each to the circuit, so that different resistor values can be experimented with.
Test Points | Test points were added to parts of the subsystem in order to measure voltage or current during testing, to avoid any unexpected mishaps and monitor the expected subsystem performance.

Table 3.2: Failure Management for the Sensing Subsystem

### 3.2 Failure Management

### 3.3 System Integration and Interfacing

To integrate the subsystem with the rest of the system ....

Interface | Description | Pins/Output
I001 | IR LED and Photodiode Cir-cuits to Motherboard +BATT and GND for power | • +BATT: IR LEDs to Motherboard Pin4 • +BATT: IR Photodiode to Motherboard Pin26 • GND: All circuits to Motherboard Pin3, Pin9, Pin15, Pin21, Pin27
I002 | Motherboard PWM to Tran-sistor Switch Circuits | • Motherboard PE8 to Transistor Q1 • Motherboard PE15 to Transistor Q2
I003 | IR Photodiode Circuit Output to Motherboard ADC Pins | • IR Photodiodes to Motherboard PA3, PA6, AB0

Table 3.3: Interfacing specifications

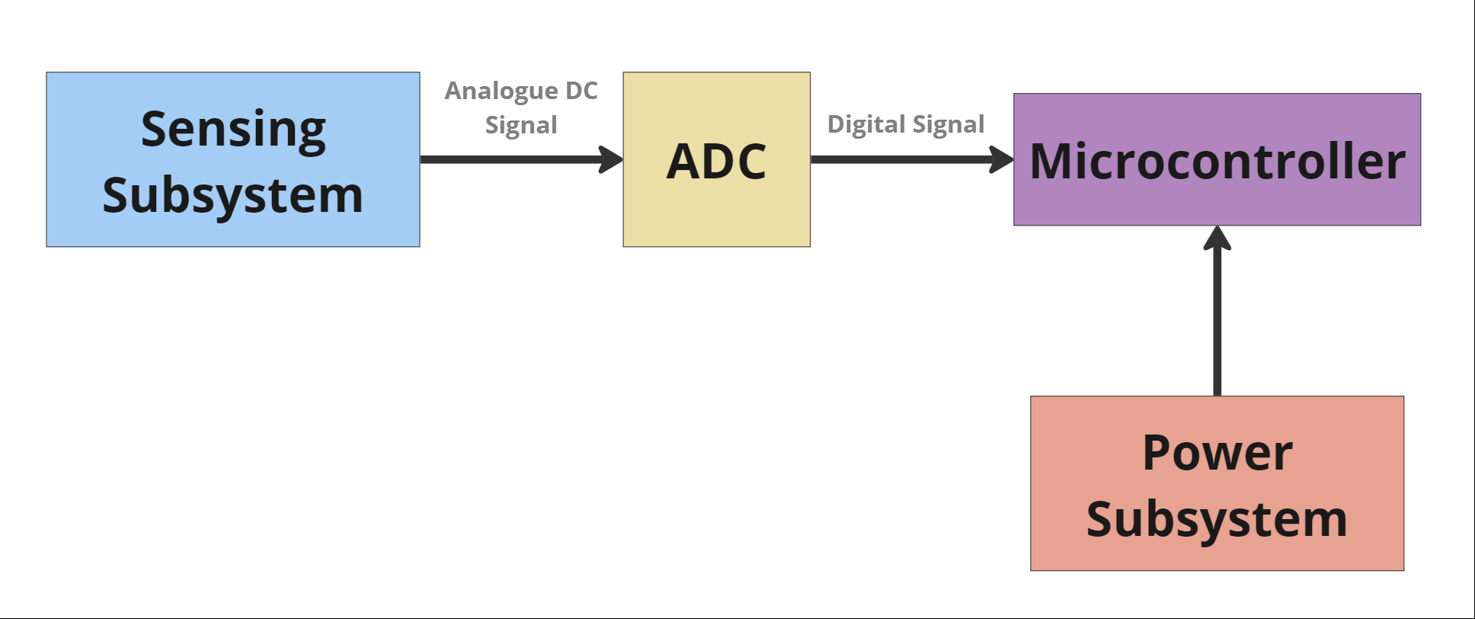
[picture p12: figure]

Figure 3.3: System Interfacing Diagram

# Chapter 4

# Acceptance Testing

### 4.1 Tests

Test
ID | Description | Testing Procedure | Pass/Fail Criteria
AT01 | IR LEDs Power on
- Connect subsystem to the motherboard
- Measure currents and voltages at test points

IR Light not visible

AT02 IR Photodiodes Power on

- Connect subsystem to the motherboard
- Measure currents and voltages at test points

No output signal while IR
LEDs are on

AT03 Subsystem output changes at the left, right, and front of the board

- Place a reflective surface in front of each sensor
- Vary surface between 6-
10cm from each sensor
- Output does not vary with distance to obstacle
- No output signal when obstacle is in front of each sensor
AT04 | Connects to motherboard

Connect subsystem to motherboard

Does not connect to/fit on motherboard

AT05 | Powers on | • Connect subsystem to the motherboard • Measure currents and volt- ages at test points
- Subsystem does not power on
- Voltage/current exceeds
maximum component ratings
AT06 | Accepted by JLCPCB | Submit PCB design and BOM files to JLCPCB shopping cart
- PCB not accepted by JL-CPCB
- Manufacturing cost exceeds $15 per board

Table 4.1: Subsystem acceptance tests

### 4.2 Critical Analysis of Testing

Table 4.2: Subsystem acceptance test results

Test
ID | Description | Result
AT01 | Powers on

4.2. Critical Analysis of Testing

### 4.2.1 AT01

This worked, this did not work. I suspect that is because of x y and z.

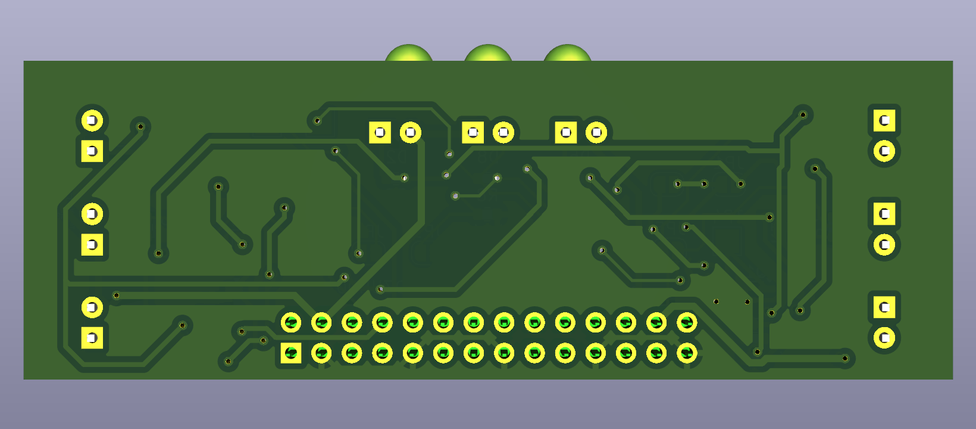
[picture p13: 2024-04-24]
Sensing Subsystem/PCB Schematics and Gerbers/BackPCB.png

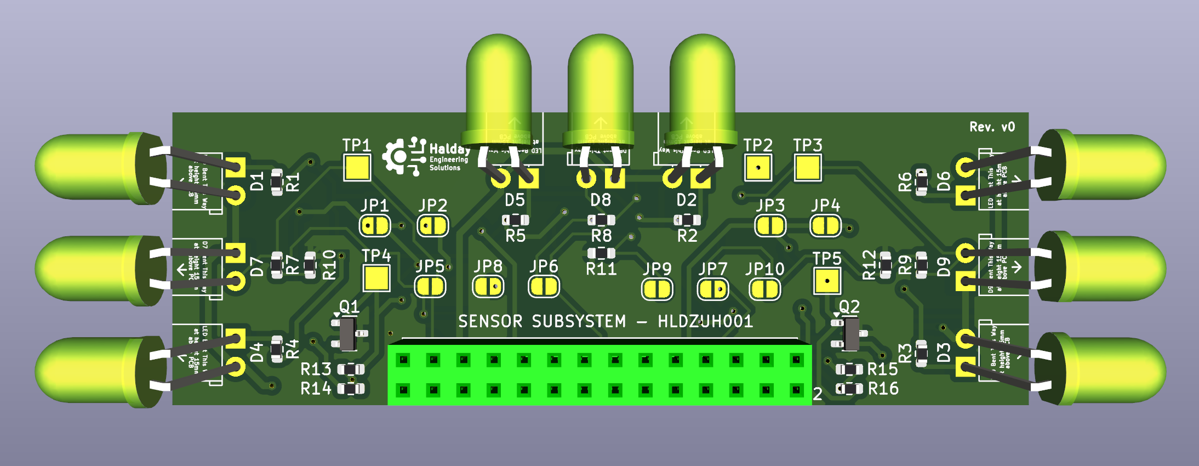
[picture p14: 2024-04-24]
Sensing Subsystem/PCB Schematics and Gerbers/FrontPCB.png

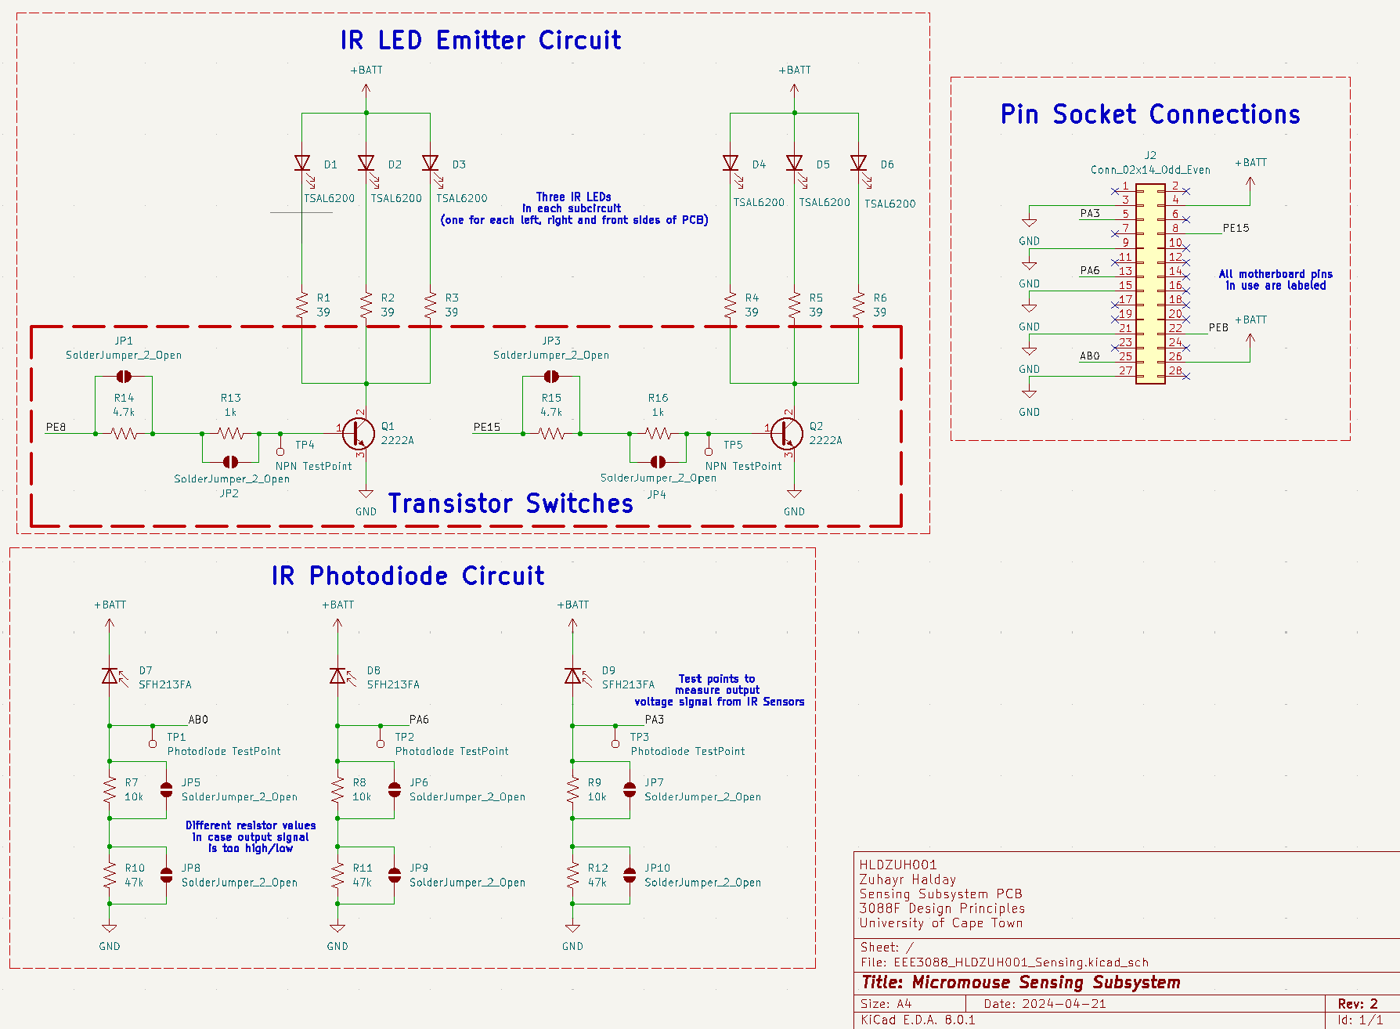
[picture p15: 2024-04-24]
Sensing Subsystem/PCB Schematics and Gerbers/Schematic.png

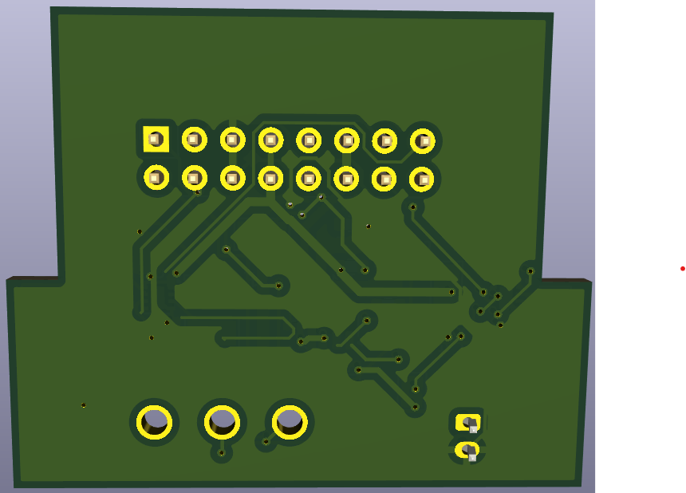
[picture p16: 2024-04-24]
Power Subsystem/PCB images/Back view.png

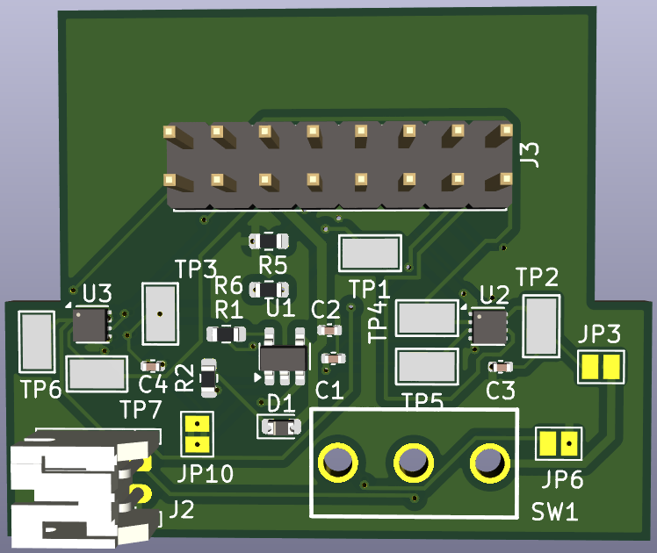
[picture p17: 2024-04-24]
Power Subsystem/PCB images/Front view.png

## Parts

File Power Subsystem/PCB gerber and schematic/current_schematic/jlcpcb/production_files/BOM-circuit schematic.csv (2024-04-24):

Comment | Designator | Footprint | LCSC
MCP73831-2-OT | U1 | SOT-23-5 | C14879
0.1uF | C3,C4 | C_0402_1005Metric | C1525
4.7uF | C1,C2 | C_0402_1005Metric | C1538
1.2k | R5 | R_0603_1608Metric | C22765
LED | D1 | D_0603_1608Metric | C2286
2k | R1 | R_0603_1608Metric | C22975
470 | R2 | R_0603_1608Metric | C23179
Slide Switch | SW1 | SW-TH_SS-12D10L5_FOOTPRINT | C319012
DRV8837 | U2,U3 | WSON-8-1EP_2x2mm_P0.5mm_EP0.9x1.6mm | C39159
3k | R6 | R_0603_1608Metric | C4211

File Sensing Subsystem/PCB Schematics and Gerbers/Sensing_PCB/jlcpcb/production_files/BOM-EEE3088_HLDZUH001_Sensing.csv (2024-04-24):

Comment | Designator | Footprint | LCSC
1k | R13,R16 | R_0603_1608Metric | C21190
39 | R1,R2,R3,R4,R5,R6 | R_0603_1608Metric | C23151
4.7k | R14,R15 | R_0603_1608Metric | C23162
10k | R7,R8,R9 | R_0603_1608Metric | C25804
47k | R10,R11,R12 | R_0603_1608Metric | C25819
D_Photo | D7,D8,D9 | LED_D5.0mm_Horizontal_O1.27mm_Z15.0mm | C2900211
IR LED | D1,D2,D3,D4,D5,D6 | LED_D5.0mm_Horizontal_O1.27mm_Z15.0mm | C55528
Q_NPN_BCE | Q1,Q2 | SOT-23 | C8512

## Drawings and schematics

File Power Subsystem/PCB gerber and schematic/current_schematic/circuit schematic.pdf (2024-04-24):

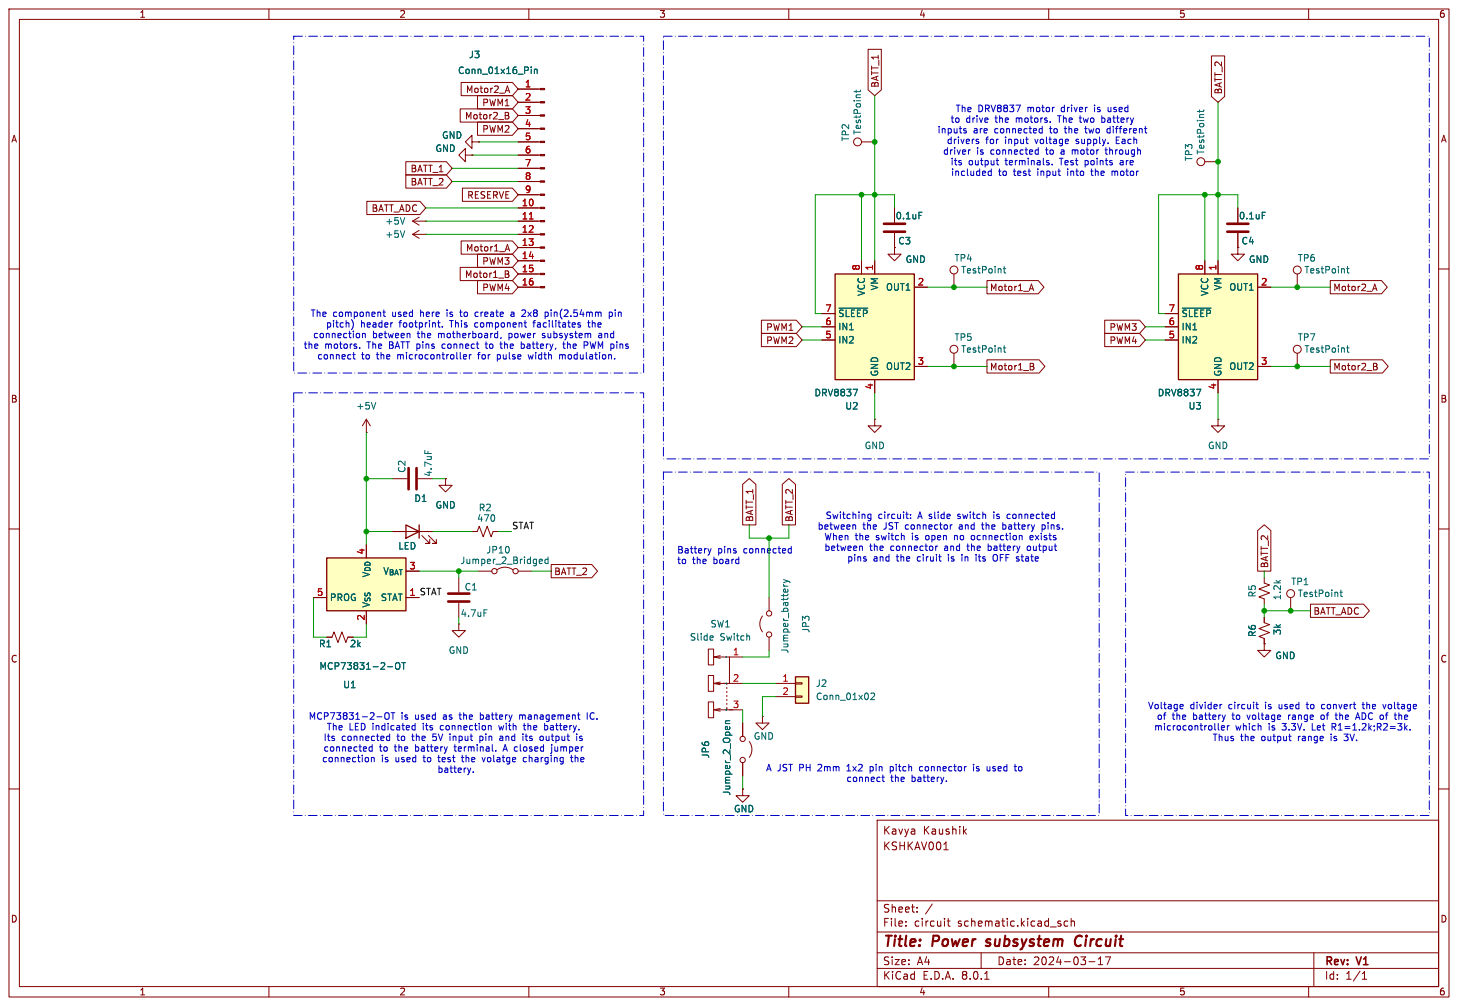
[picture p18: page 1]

The DRV8837 motor driver is used
to drive the motors. The two battery

the motors. The BATT pins connect to the battery, the PWM pins

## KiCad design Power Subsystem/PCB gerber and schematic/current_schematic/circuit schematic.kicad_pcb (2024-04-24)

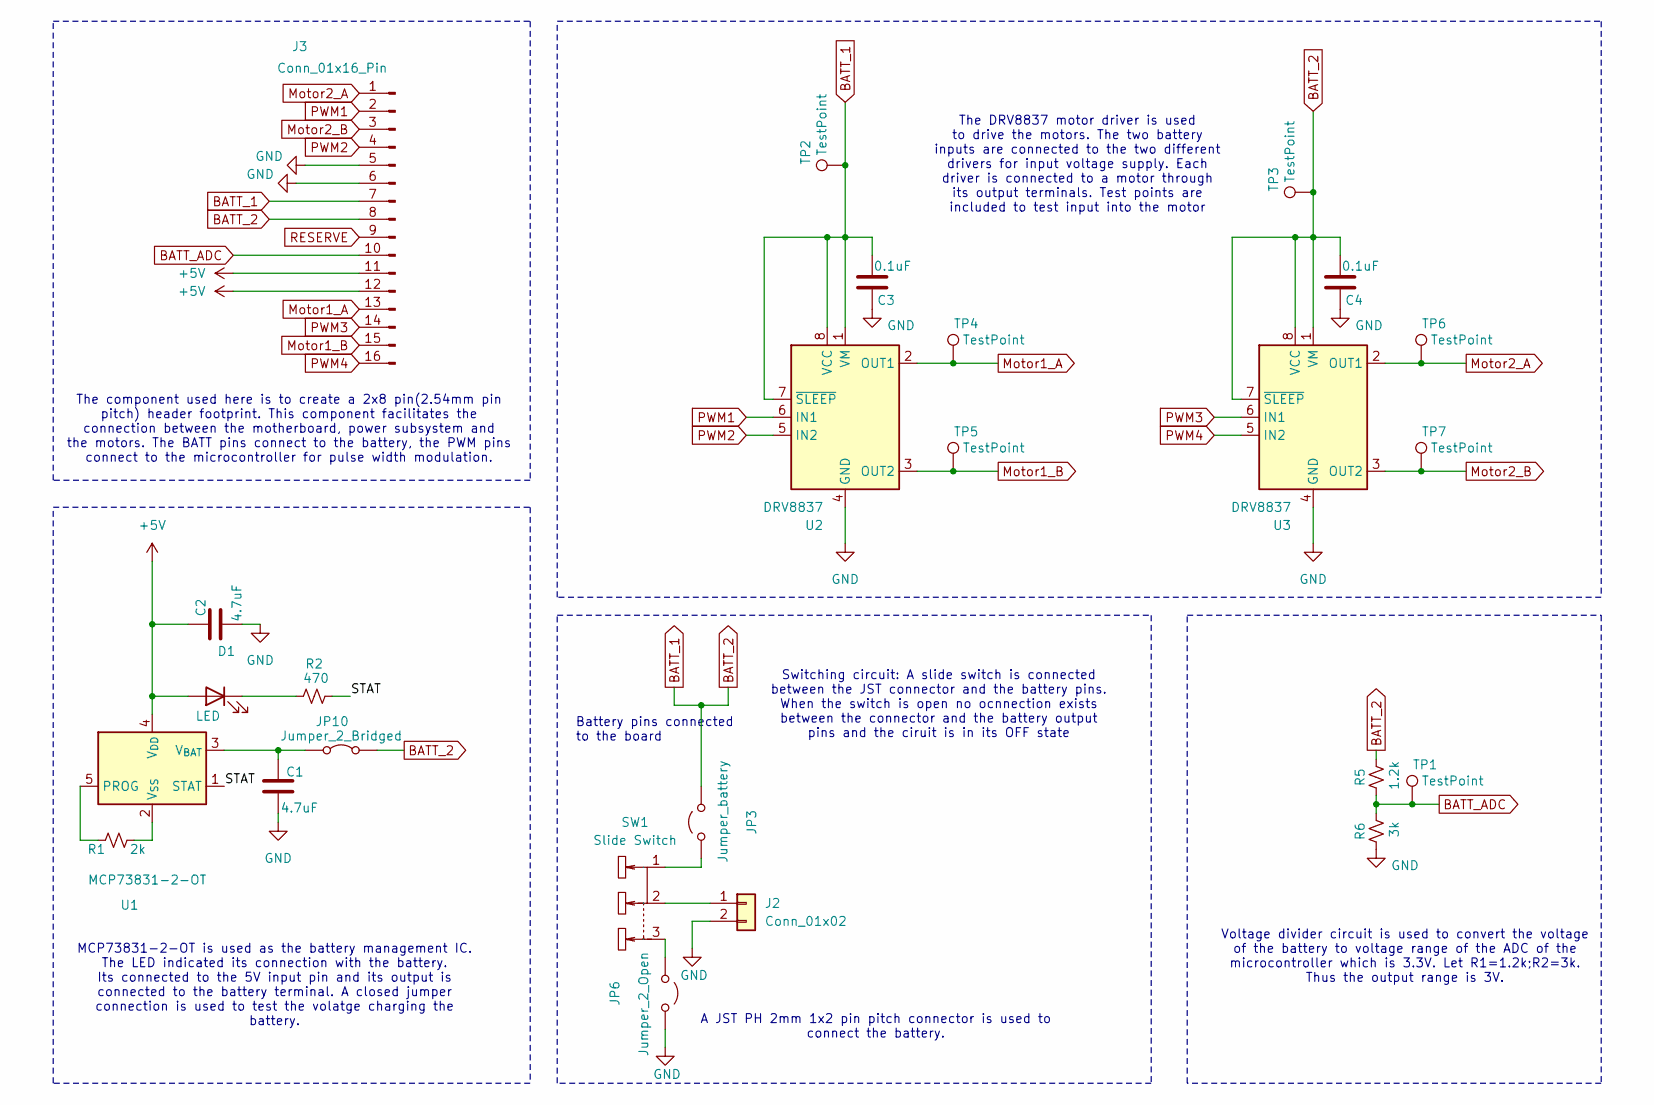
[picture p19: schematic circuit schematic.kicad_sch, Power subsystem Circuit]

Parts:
C1, C2: 4.7uF; C_0402_1005Metric; LCSC C1538
C3, C4: 0.1uF; C_0402_1005Metric; LCSC C1525
D1: LED; D_0603_1608Metric; LCSC C2286
J2: Conn_01x02; JST_PH_S2B-PH-K_1x02_P2.00mm_Horizontal
J3: Conn_01x16_Pin; PinHeader_2x08_P2.54mm_Vertical
JP3: Jumper_battery; SolderJumper-2_P1.3mm_Open_Pad1.0x1.5mm
JP6: Jumper_2_Open; SolderJumper-2_P1.3mm_Open_Pad1.0x1.5mm
JP10: Jumper_2_Bridged; SolderJumper-2_P1.3mm_Bridged2Bar_Pad1.0x1.5mm
R1: 2k; R_0603_1608Metric; LCSC C22975
R2: 470; R_0603_1608Metric; LCSC C23179
R5: 1.2k; R_0603_1608Metric; LCSC C22765
R6: 3k; R_0603_1608Metric; LCSC C4211
SW1: Slide Switch; SW-TH_SS-12D10L5_FOOTPRINT; LCSC C319012
TP1, TP2, TP3, TP4, TP5, TP6, TP7: TestPoint; TestPoint_Keystone_5015_Micro-Minature
U1: MCP73831-2-OT; SOT-23-5; LCSC C14879
U2, U3: DRV8837; WSON-8-1EP_2x2mm_P0.5mm_EP0.9x1.6mm; LCSC C39159

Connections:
+5V: C2.1, D1.2 (A), J3.11, J3.12, U1.4 (V_{DD})
/STAT: R2.2, U1.1 (STAT)
BATT_1: C3.2, C4.2, J3.7, J3.8, JP3.2 (B), JP10.2 (B), R5.2, TP2.1, TP3.1, U2.1 (VM), U2.7 (~SLEEP), U2.8 (VCC), U3.1 (VM), U3.7 (~SLEEP), U3.8 (VCC)
BATT_ADC: J3.10, R5.1, R6.2, TP1.1
GND: C1.2, C2.2, C3.1, C4.1, J2.2, J3.5, J3.6, JP6.2 (B), R6.1, U2.4 (GND), U2.9 (GND), U3.4 (GND), U3.9 (GND)
Motor1_A: J3.13, TP4.1, U2.2 (OUT1)
Motor1_B: J3.15, TP5.1, U2.3 (OUT2)
Motor2_A: J3.1, TP6.1, U3.2 (OUT1)
Motor2_B: J3.3, TP7.1, U3.3 (OUT2)
unnamed: D1.1 (K), R2.1
unnamed: J2.1, SW1.2
unnamed: JP3.1 (A), SW1.1
unnamed: JP6.1 (A), SW1.3
unnamed: C1.1, JP10.1 (A), U1.3 (V_{BAT})
unnamed: R1.1, U1.5 (PROG)
unnamed: R1.2, U1.2 (V_{SS})
PWM1: J3.2, U2.6 (IN1)
PWM2: J3.4, U2.5 (IN2)
PWM3: J3.14, U3.6 (IN1)
PWM4: J3.16, U3.5 (IN2)
RESERVE: J3.9

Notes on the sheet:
Switching circuit: A slide switch is connected between the JST connector and the battery pins. When the switch is open no ocnnection exists between the connector and the battery output pins and the ciruit is in its OFF state
MCP73831-2-OT is used as the battery management IC. The LED indicated its connection with the battery. Its connected to the 5V input pin and its output is connected to the battery terminal. A closed jumper connection is used to test the volatge charging the battery.
A JST PH 2mm 1x2 pin pitch connector is used to connect the battery.
Battery pins connected to the board
Voltage divider circuit is used to convert the voltage of the battery to voltage range of the ADC of the microcontroller which is 3.3V. Let R1=1.2k;R2=3k. Thus the output range is 3V.
The component used here is to create a 2x8 pin(2.54mm pin pitch) header footprint. This component facilitates the connection between the motherboard, power subsystem and the motors. The BATT pins connect to the battery, the PWM pins connect to the microcontroller for pulse width modulation.
The DRV8837 motor driver is used to drive the motors. The two battery inputs are connected to the two different drivers for input voltage supply. Each driver is connected to a motor through its output terminals. Test points are included to test input into the motor

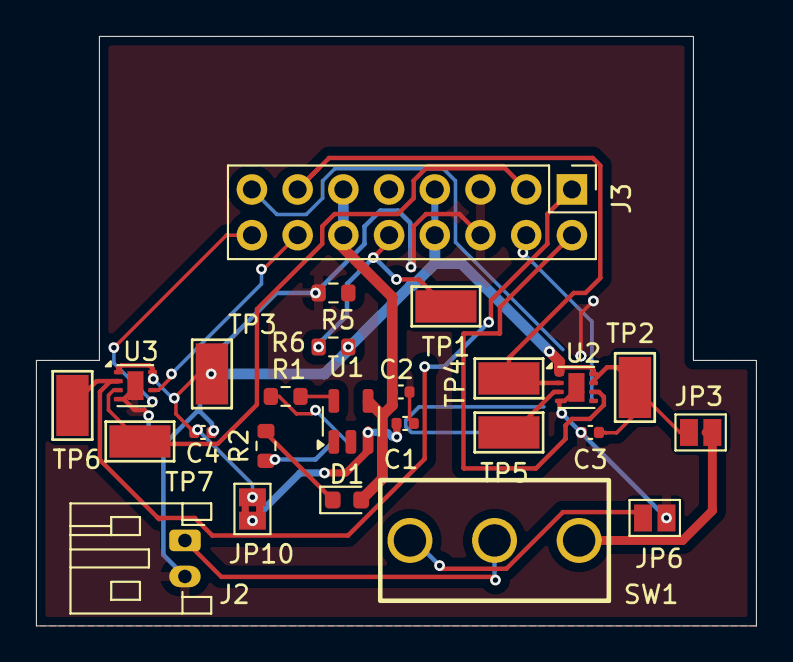
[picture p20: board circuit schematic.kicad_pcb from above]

Board: 2 copper layers, 40.0 x 32.8 mm, 25 parts (0 on the bottom side), 20 nets.

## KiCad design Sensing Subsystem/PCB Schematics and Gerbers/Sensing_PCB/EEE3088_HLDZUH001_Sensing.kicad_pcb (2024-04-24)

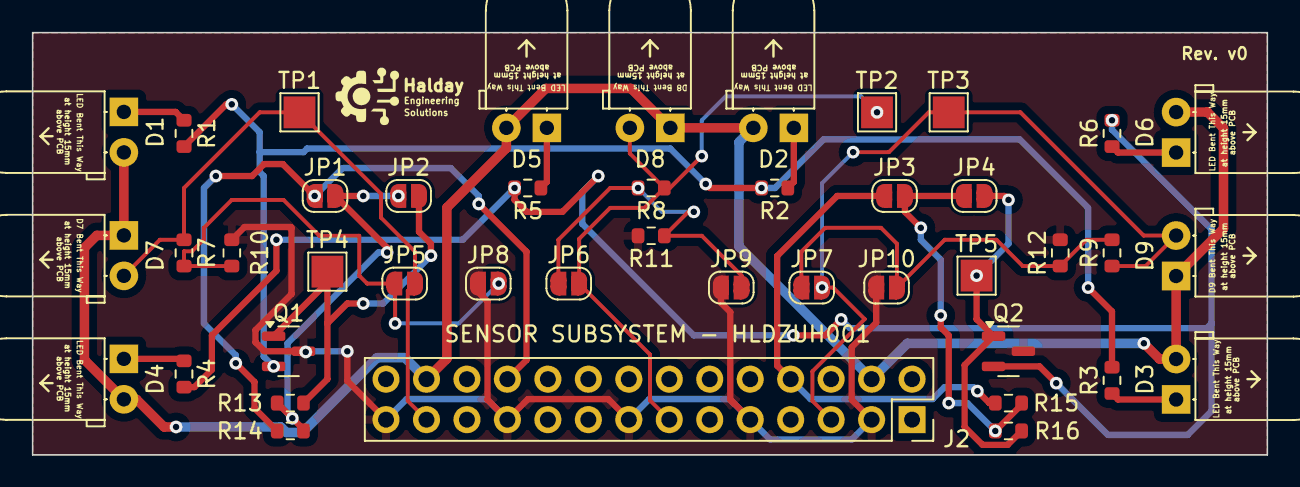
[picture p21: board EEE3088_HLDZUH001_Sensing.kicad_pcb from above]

Board: 2 copper layers, 77.5 x 26.5 mm, 43 parts (0 on the bottom side), 22 nets.

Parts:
D1, D2, D3, D4, D5, D6: IR LED; LED_D5.0mm_Horizontal_O1.27mm_Z15.0mm
D7, D8, D9: D_Photo; LED_D5.0mm_Horizontal_O1.27mm_Z15.0mm
J2: Conn_02x14_Odd_Even; PinSocket_2x14_P2.54mm_Vertical
JP1, JP2, JP3, JP4, JP5, JP6, JP7, JP8, JP9, JP10: SolderJumper_2_Open; SolderJumper-2_P1.3mm_Open_RoundedPad1.0x1.5mm
Q1, Q2: Q_NPN_BCE; SOT-23
R1, R2, R3, R4, R5, R6: 39; R_0603_1608Metric
R7, R8, R9: 10k; R_0603_1608Metric
R10, R11, R12: 47k; R_0603_1608Metric
R13, R16: 1k; R_0603_1608Metric
R14, R15: 4.7k; R_0603_1608Metric
TP1, TP2, TP3, TP4, TP5: TestPoint; TestPoint_Pad_2.0x2.0mm

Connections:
+BATT: D1.2 (A), D2.2 (A), D3.2 (A), D4.2 (A), D5.2 (A), D6.2 (A), D7.1 (K), D8.1 (K), D9.1 (K), J2.4, J2.26
/AB0: D7.2 (A), J2.25, JP5.2 (B), R7.1, TP1.1
/PA3: D9.2 (A), J2.5, JP7.2 (B), R9.1, TP3.1
/PA6: D8.2 (A), J2.13, JP6.2 (B), R8.1, TP2.1
/PE8: J2.22, JP1.1 (A), R14.1
/PE15: J2.8, JP3.1 (A), R15.1
GND: J2.3, J2.9, J2.15, J2.21, J2.27, JP8.1 (A), JP9.1 (A), JP10.1 (A), Q1.3 (E), Q2.3 (E), R10.2, R11.2, R12.2
unnamed: D1.1 (K), R1.1
unnamed: D2.1 (K), R2.1
unnamed: D3.1 (K), R3.1
unnamed: D4.1 (K), R4.1
unnamed: D5.1 (K), R5.1
unnamed: D6.1 (K), R6.1
unnamed: JP1.2 (B), JP2.1 (A), R13.1, R14.2
unnamed: JP2.2 (B), Q1.1 (B), R13.2, TP4.1
unnamed: JP3.2 (B), JP4.1 (A), R15.2, R16.1
unnamed: JP4.2 (B), Q2.1 (B), R16.2, TP5.1
unnamed: JP5.1 (A), JP8.2 (B), R7.2, R10.1
unnamed: JP6.1 (A), JP9.2 (B), R8.2, R11.1
unnamed: JP7.1 (A), JP10.2 (B), R9.2, R12.1
unnamed: Q1.2 (C), R1.2, R2.2, R3.2
unnamed: Q2.2 (C), R4.2, R5.2, R6.2

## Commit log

2024-04-24 Uploaded Sensing Subsystem folder
    [BOM-EEE3088_HLDZUH001_Sensing.csv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]
2024-04-24 Resistor Datasheet (All resistors)
2024-05-17 Uploaded STM32 Sensing Code for ADC and PWM
